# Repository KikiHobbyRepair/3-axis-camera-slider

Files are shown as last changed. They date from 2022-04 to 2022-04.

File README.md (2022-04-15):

# 3-axis-camera-slider
My newest DIY project is a 3 Axis motorised camera slicer. It is capable of handling smaller DSLR cameras and phones. It is portable because can be operated from a battery or alternatively from a DC power supply.

Link to the Youtube video: https://www.youtube.com/watch?v=ZBGcE2LZntI

I will also post a video later on about the full build process. I will put a link here as soon as it is published.

Parts list:
- 3D printed parts (preferred: PETG)
- openbuilds V wheel gentry. Most probably these are mostly the same but this is what I used: https://www.ebay.com/itm/403322339944
- 2040 V slot aluminum extrusion profile (I used 600mm long)
- 3 pcs Nema 17 stepper motors (I used 2pcs 0,9deg 2A and 1pc 1,8deg 2A version). High torque is needed especially for the tiliting mechanism
- 3pcs TMC2209 stepper motor drivers  https://www.aliexpress.com/item/33025652788.html?gatewayAdapt=glo2fra&spm=a2g0o.order_list.0.0.72a81802hnKEYC
- Bigtreetech extension board https://www.aliexpress.com/item/4001286167374.html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
- Arduino Nano (5V)
- 1,3" OLED screen (SPI version) https://www.aliexpress.com/item/32683739839.html?spm=a2g0o.order_list.0.0.72a81802AinbYI
- Rotary encoder: https://www.aliexpress.com/item/10000056483250.html?spm=a2g0o.order_list.0.0.72a81802AinbYI
- Momentary pushbutton: https://www.aliexpress.com/item/32965284265.html?spm=a2g0o.order_list.0.0.72a81802AinbYI
- GT2 Belt 6mm wide
- 20 teeth GT2 pulley with 5mm inner dia
- 20 teeth GT2 idler with 5mm inner dia
- M3 and M5 allen screws in different length (buy an assortment kit)
- M5 hammerhead nuts or T slot nuts
- M5 and M3 rectangluar nuts https://www.aliexpress.com/item/32964308882.html?spm=a2g0o.order_list.0.0.72a81802hnKEYC
- Some wires
- Rubber band for phone mount https://www.aliexpress.com/item/32751762287.html?spm=a2g0o.order_list.0.0.72a81802hnKEYC
- F623ZZ bearing 1 pcs
- Flange shaft coupler 2pcs (I have designed a 3D printed version too (STL available) but I prefer the metal here) https://www.amazon.de/gp/product/B0833PTFZM/ref=ppx_yo_dt_b_asin_title_o02_s00?ie=UTF8&psc=1
- etc

Buy Me a Coffe. If you find my work useful and valuable you can support the channel on the following link: https://www.buymeacoffee.com/kikihobbyrepair
3D file

DIY 3 Axis Motorized Camera Slider Thumbnail

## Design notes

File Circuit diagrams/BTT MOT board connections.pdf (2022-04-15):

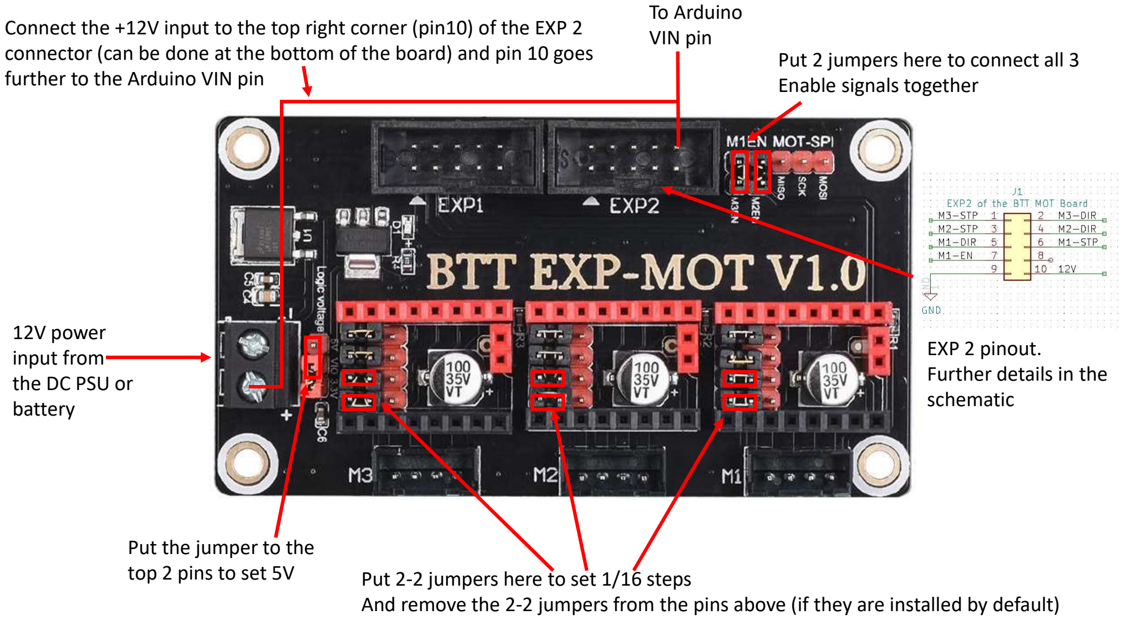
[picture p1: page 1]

Put 2 jumpers here to connect all 3 Enable signals together

Put 2-2 jumpers here to set 1/16 steps
And remove the 2-2 jumpers from the pins above (if they are installed by default)

Put the jumper to the
top 2 pins to set 5V

Connect the +12V input to the top right corner (pin10) of the EXP 2 connector (can be done at the bottom of the board) and pin 10 goes further to the Arduino VIN pin

EXP 2 pinout.
Further details in the
schematic

12V power
input from
the DC PSU or
battery

To Arduino
VIN pin

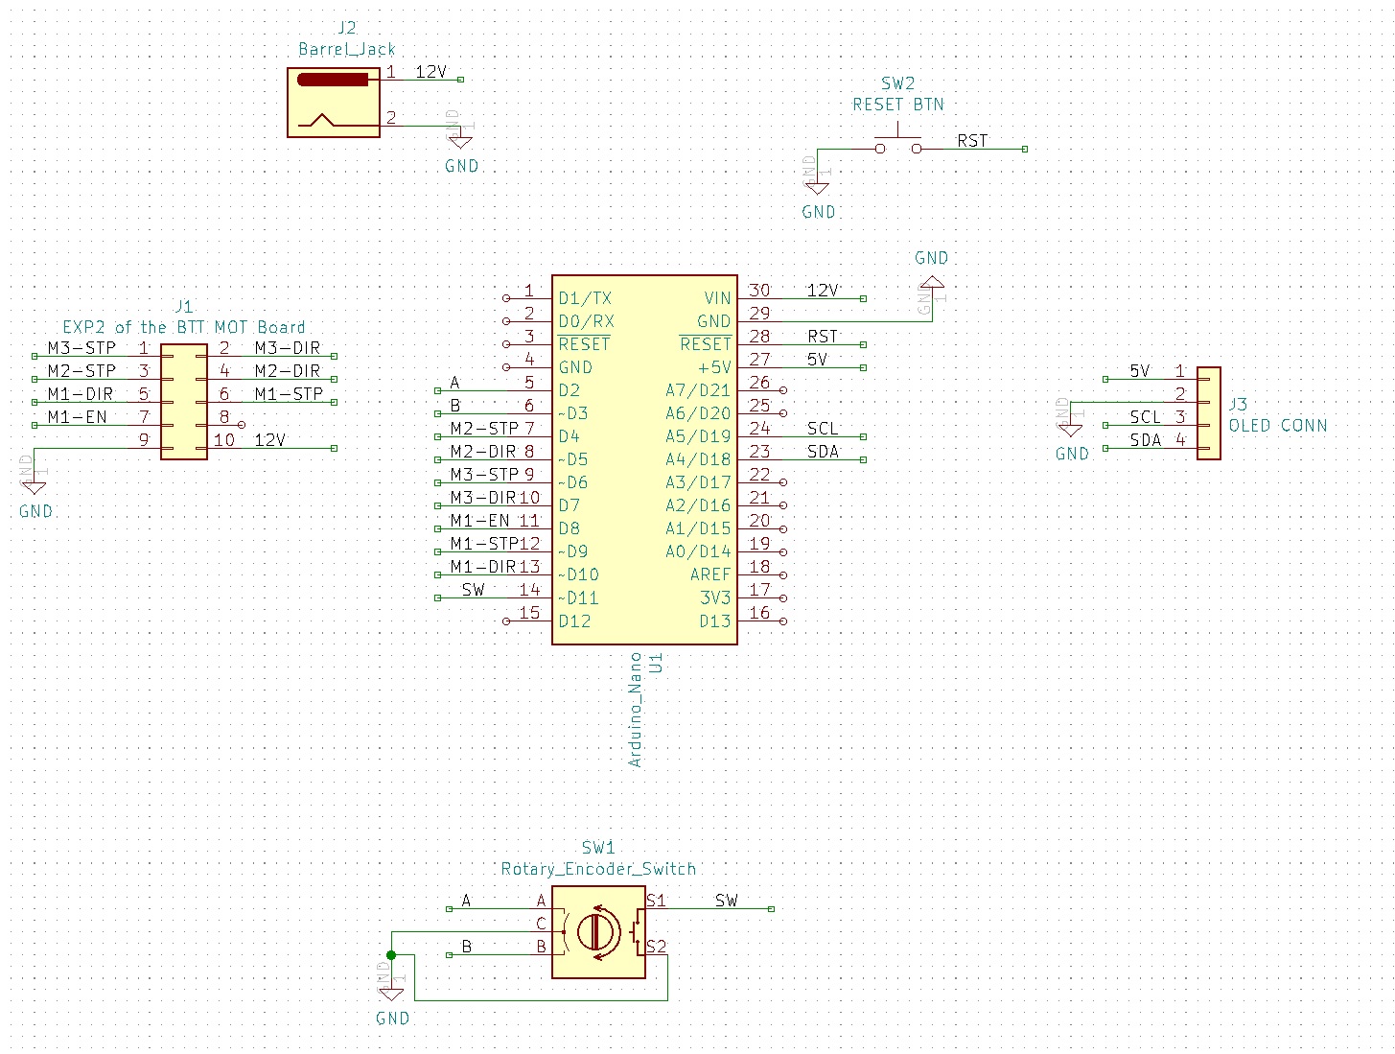
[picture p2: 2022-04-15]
Circuit diagrams/Schematic.jpg

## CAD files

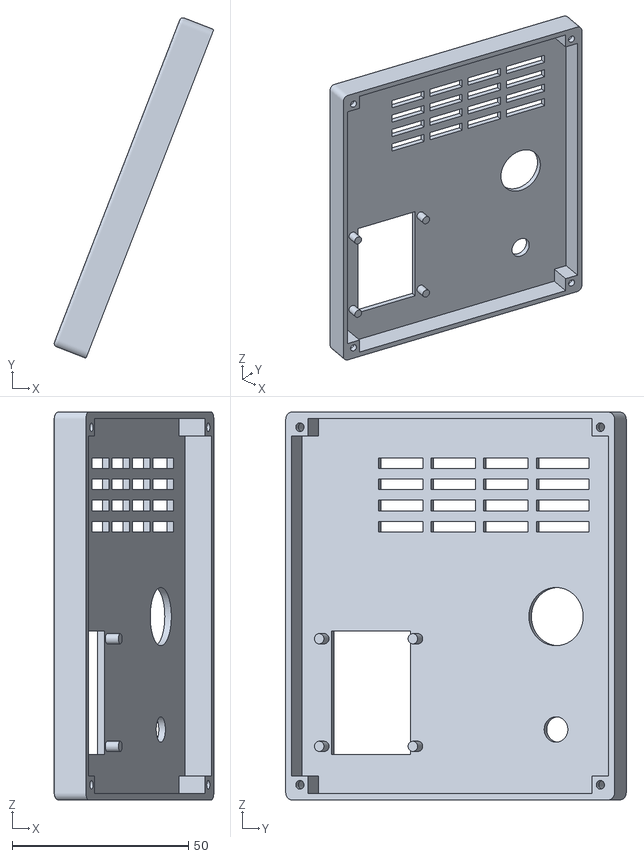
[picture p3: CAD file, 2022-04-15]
STL files/Box top.stl
45.3 x 96.5 x 110.0

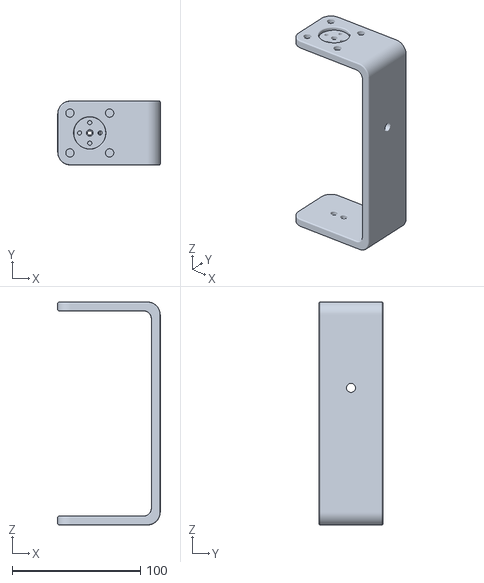
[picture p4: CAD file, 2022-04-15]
STL files/Camera mount.stl
80.0 x 50.0 x 174.0

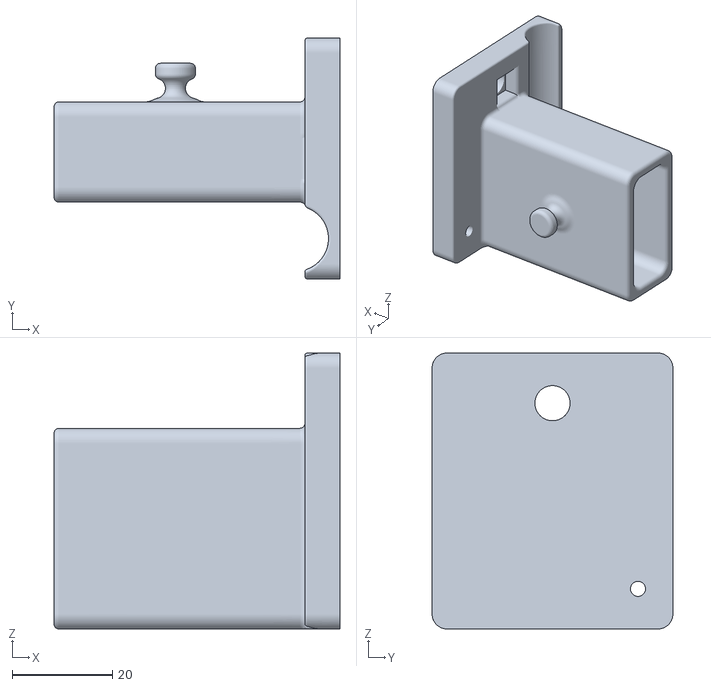
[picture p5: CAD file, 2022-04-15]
STL files/Phone holder bottom.stl
57.0 x 48.0 x 55.0

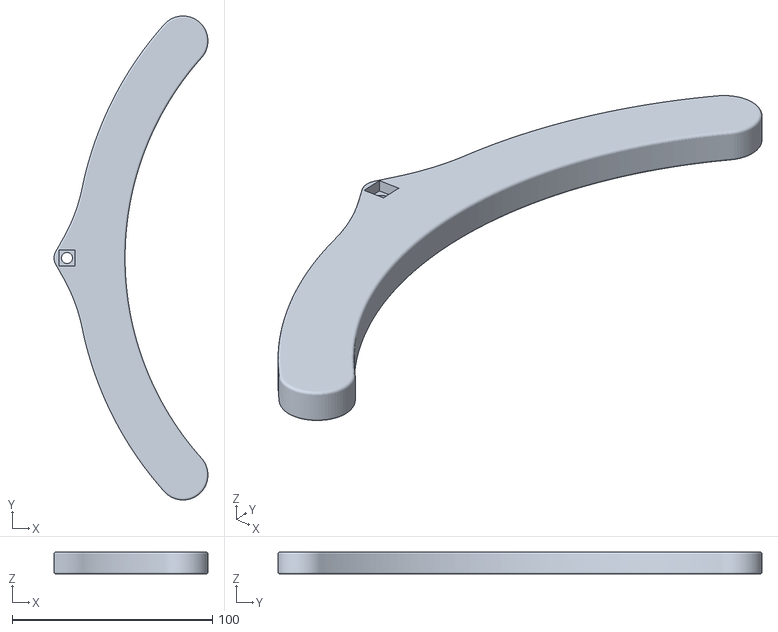
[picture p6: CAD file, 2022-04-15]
STL files/Leg 1.stl
76.9 x 241.7 x 10.9

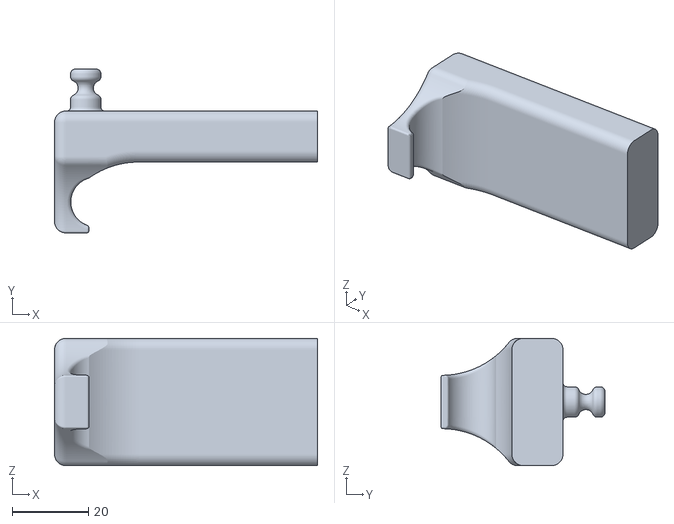
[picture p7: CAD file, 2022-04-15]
STL files/Phone holder top.stl
69.0 x 43.0 x 33.4

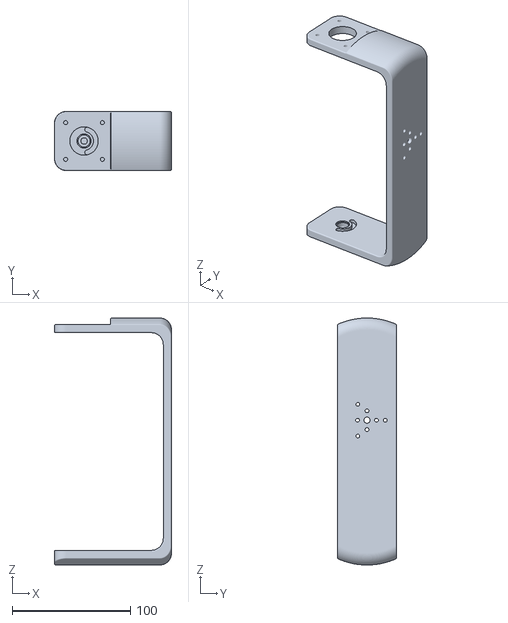
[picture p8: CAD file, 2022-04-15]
STL files/Top stepper holder.stl
99.0 x 50.0 x 208.9

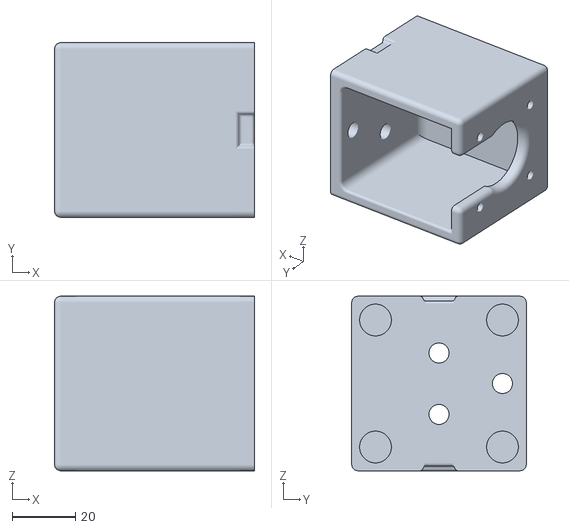
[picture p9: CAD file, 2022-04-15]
STL files/Bottom stepper holder 53mm inner.stl
63.0 x 55.0 x 55.0

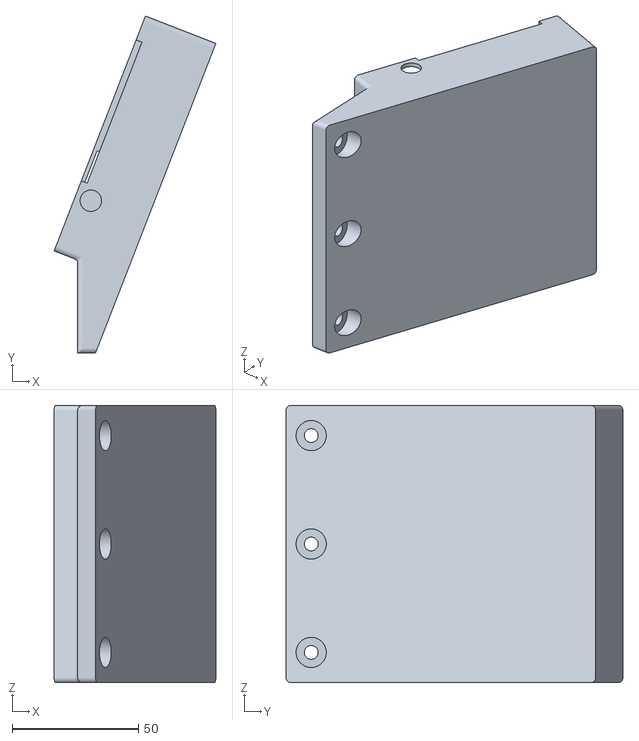
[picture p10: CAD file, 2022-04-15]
STL files/Box bottom.stl
64.2 x 133.7 x 110.0

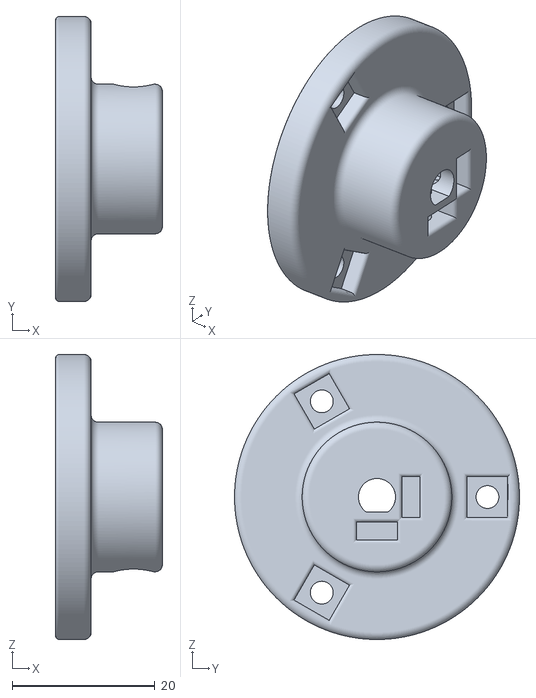
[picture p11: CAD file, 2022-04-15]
STL files/Shaft coupler.stl
15.0 x 40.0 x 40.0

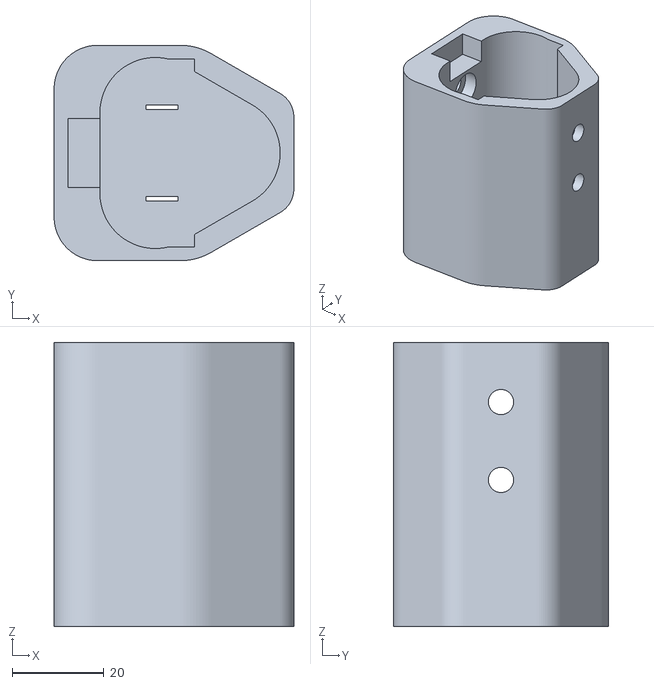
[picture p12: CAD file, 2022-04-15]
STL files/AEG battery holder.stl
52.4 x 47.0 x 62.0

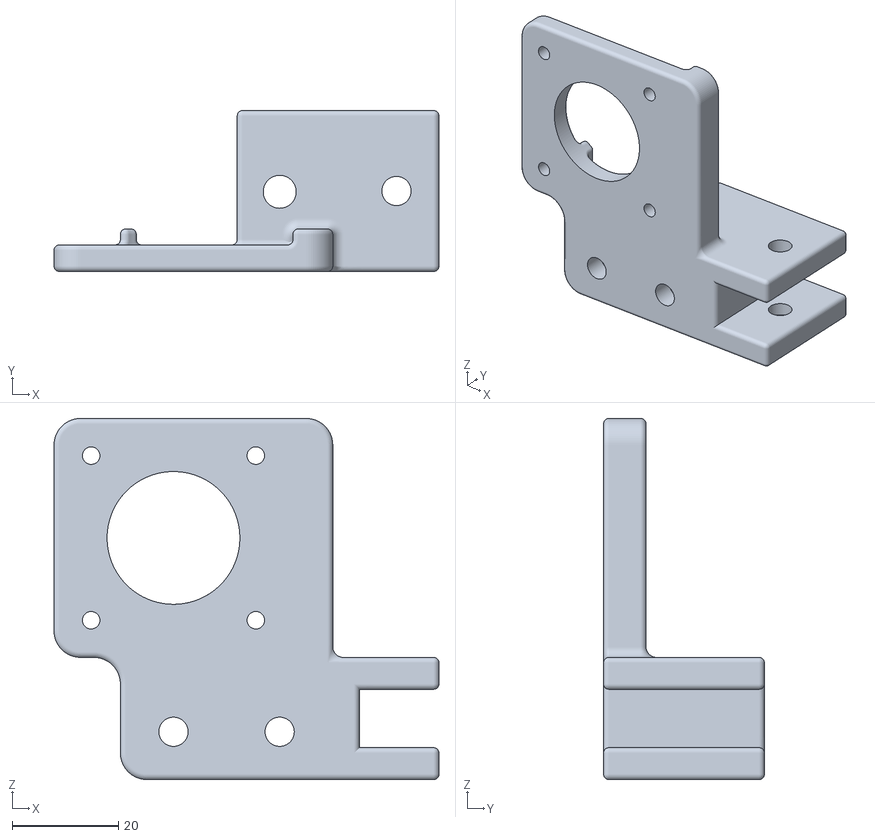
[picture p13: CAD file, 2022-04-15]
STL files/X stepper holder.stl
72.5 x 30.3 x 68.0

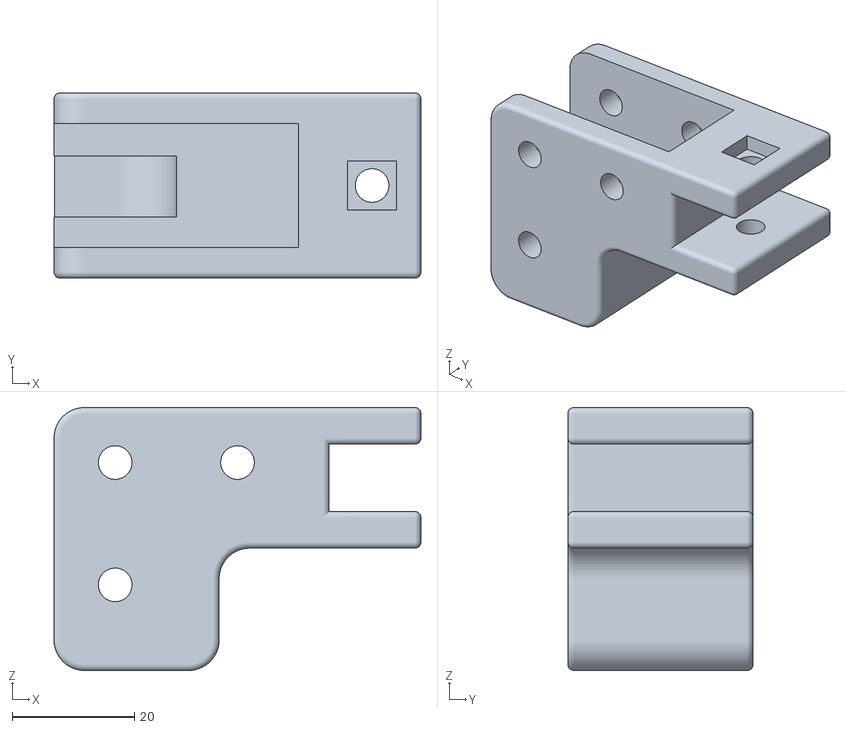
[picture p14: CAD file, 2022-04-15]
STL files/X idler holder.stl
60.0 x 30.3 x 43.0

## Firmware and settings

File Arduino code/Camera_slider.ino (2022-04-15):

//3 axis Camera Slider --- Kiki Hobby Repair
//Under development - USE IT AT YOUR OWN RISK!


#include <Arduino.h>
#include <Rotary.h>
#include <OneButton.h> 
#include <SpeedyStepper.h>
#include <U8g2lib.h>
#include <stdint.h>


Rotary r = Rotary(2, 3);
U8G2_SH1106_128X64_NONAME_1_HW_I2C u8g2(U8G2_R0, /* reset=*/ U8X8_PIN_NONE);  

#define enablePin       8                      //Motor enable pin
OneButton button(11,true);                     //Rotary Encoder Button
#define stepsPerMm      80                     //Slider step/mm (with 1.8deg motor)
#define stepPerDeg      17.77778               //rotate/tilt steps/degree (with 0.9deg motor)

const int MOTOR1_STEP_PIN = 9;
const int MOTOR1_DIRECTION_PIN = 10;
const int MOTOR2_STEP_PIN = 4;
const int MOTOR2_DIRECTION_PIN = 5;
const int MOTOR3_STEP_PIN = 6;
const int MOTOR3_DIRECTION_PIN = 7;

SpeedyStepper stepper1;
SpeedyStepper stepper2;
SpeedyStepper stepper3;

unsigned char result;
float encPos = 0;
int encMin = 0;
int encMax = 4;
int encSteps = 1;
int enter = 0;
int val = 0;
int slideDist = 0;
float rotAngle = 0;
float moveSpeed = 0;
float rotSpeed = 0;
float tiltSpeed = 0;
float tiltAngle = 0;



void setup() {
  
  u8g2.begin();
  u8g2.enableUTF8Print();
  pinMode(enablePin, OUTPUT);                        
  r.begin();
  PCICR |= (1 << PCIE2);
  PCMSK2 |= (1 << PCINT18) | (1 << PCINT19);
  sei();
  
  button.attachClick(click);
  stepper1.connectToPins(MOTOR1_STEP_PIN, MOTOR1_DIRECTION_PIN);
  stepper2.connectToPins(MOTOR2_STEP_PIN, MOTOR2_DIRECTION_PIN);
  stepper3.connectToPins(MOTOR3_STEP_PIN, MOTOR3_DIRECTION_PIN);
  stepper1.setStepsPerMillimeter(80);
  stepper2.setStepsPerRevolution(6400);
  stepper3.setStepsPerRevolution(6400);
  stepper1.setAccelerationInMillimetersPerSecondPerSecond(50);
  stepper2.setAccelerationInMillimetersPerSecondPerSecond(50);
  stepper3.setAccelerationInMillimetersPerSecondPerSecond(50);
  
  
}

void loop() {
  enter = 0;
  encMin = 0;
  encMax = 4;
  encSteps = 1;
  digitalWrite(enablePin, LOW);
  button.tick();
  
   u8g2.firstPage();
      do {
        
        u8g2.setFont(u8g2_font_osb18_tr);
        
           
        if (encPos == 0) {
          u8g2.setCursor(40, 40);  
          u8g2.print("Slide");
          if (enter == 1)
            {                     
              slide();
            }
          }
        
        else if  (encPos == 1) {
          
          u8g2.setCursor(15, 30);
          u8g2.print("Slide and"); 
          u8g2.setCursor(30, 55);
          u8g2.print("Rotate"); 
          if (enter == 1)
            {                     
              slideAndRotate();
            }   
          }
          
           else if  (encPos == 2) {
           u8g2.setCursor(40, 20);
          u8g2.print("Slide"); 
          u8g2.setCursor(5, 40);
          u8g2.print("Rotate and"); 
          u8g2.setCursor(46, 64);
          u8g2.print("Tilt"); 
          if (enter == 1)
            {                     
              slideAndRotateAndTilt();
            }  
          
          } 
        
          else if  (encPos == 3) {
           u8g2.setCursor(15, 30);
          u8g2.print("Slide and"); 
          u8g2.setCursor(46, 55);
          u8g2.print("Tilt"); 
          if (enter == 1)
            {                     
              slideAndTilt();
            } 
          }
        
          else if  (encPos == 4) {
           u8g2.setCursor(27, 30);
          u8g2.print("Object"); 
          u8g2.setCursor(13, 55);
          u8g2.print("Tracking");
          if (enter == 1)
            {                     
              objectTracking();
            } 
              
          }
        
   
      } while (u8g2.nextPage());    
          
}



ISR(PCINT2_vect) {
  result = r.process();
  if (result == DIR_NONE) {
    
  }
  else if (result == DIR_CW && encPos < encMax) {
    encPos = encPos + encSteps;
  }
  else if (result == DIR_CCW && encPos > encMin) {
    encPos = encPos - encSteps;
  }
  
}

void click()
  {
  enter = 1;
  }

void slide()
{
 encPos = 0;
 enter = 0;
 while (enter == 0)
  {
  button.tick();
  encMin = -450;
  encMax = 450;
  encSteps = 25;
  u8g2.firstPage();
      do {
  
          u8g2.setFont(u8g2_font_osb18_tr);
          u8g2.setCursor(15, 20);
          u8g2.print("Distance"); 
          u8g2.setCursor(15, 50);
          u8g2.print(encPos, 0);
          u8g2.setCursor(80, 50);
          u8g2.print("mm"); 
          

          slideDist = encPos;
          } while (u8g2.nextPage());
    
  }
    enter = 0;
    encPos = 10;

    
  while (enter == 0)
  {
  button.tick();
  encMin = 10;
  encMax = 3600;
  encSteps = 10;
  u8g2.firstPage();
      do {
  
          u8g2.setFont(u8g2_font_osb18_tr);
          u8g2.setCursor(15, 20);
          u8g2.print("Duration"); 
          u8g2.setCursor(15, 50);
          u8g2.print(encPos, 0);
          u8g2.setCursor(80, 50);
          u8g2.print("sec"); 
          moveSpeed = slideDist / encPos;
          } while (u8g2.nextPage());
  } 
  u8g2.firstPage();
      do {
  
          u8g2.setFont(u8g2_font_osb18_tr);
          u8g2.setCursor(15, 40);
          u8g2.print("Moving"); 
          
          } while (u8g2.nextPage());
  stepper1.setSpeedInMillimetersPerSecond(abs(moveSpeed));
  stepper1.setupRelativeMoveInMillimeters(slideDist);
    
  while(!stepper1.motionComplete()) 
        {
          stepper1.processMovement();
          
      
        }
  enter = 0;
  encPos = 0;
  moveSpeed = 0;
  slideDist = 0;
  
  }

  
void slideAndRotate()
{

 encPos = 0;
 enter = 0;
 while (enter == 0)
  {
  button.tick();
  encMin = -450;
  encMax = 450;
  encSteps = 25;
  u8g2.firstPage();
      do {
  
          u8g2.setFont(u8g2_font_osb18_tr);
          u8g2.setCursor(15, 20);
          u8g2.print("Distance"); 
          u8g2.setCursor(15, 50);
          u8g2.print(encPos, 0);
          u8g2.setCursor(80, 50);
          u8g2.print("mm"); 
          slideDist = encPos;
          } while (u8g2.nextPage());
    
  }
    enter = 0;
    encPos = 0;
    
  while (enter == 0)
  {
  button.tick();
  encMin = -120;
  encMax =  120;
  encSteps = 10;
  u8g2.firstPage();
      do {
  
          u8g2.setFont(u8g2_font_osb18_tr);
          u8g2.setCursor(0, 20);
          u8g2.print("Rot. Angle"); 
          u8g2.setCursor(15, 50);
          u8g2.print(encPos, 0);
          u8g2.setCursor(80, 50);
          u8g2.print("deg"); 
          rotAngle = encPos/360;
          } while (u8g2.nextPage());
  }

        enter = 0;
        encPos = 10;
        
  while (enter == 0)
  {
  button.tick();
  encMin = 10;
  encMax = 3600;
  encSteps = 10;
  u8g2.firstPage();
      do {
  
          u8g2.setFont(u8g2_font_osb18_tr);
          u8g2.setCursor(15, 20);
          u8g2.print("Duration"); 
          u8g2.setCursor(15, 50);
          u8g2.print(encPos, 0);
          u8g2.setCursor(80, 50);
          u8g2.print("sec"); 
          moveSpeed = slideDist / encPos;
          rotSpeed = rotAngle / encPos;
          } while (u8g2.nextPage());
  } 
  u8g2.firstPage();
      do {
  
          u8g2.setFont(u8g2_font_osb18_tr);
          u8g2.setCursor(15, 40);
          u8g2.print("Moving"); 
          
          } while (u8g2.nextPage());
  stepper1.setSpeedInMillimetersPerSecond(abs(moveSpeed));
  stepper1.setupRelativeMoveInMillimeters(slideDist);
  stepper2.setSpeedInRevolutionsPerSecond(abs(rotSpeed));
  stepper2.setupRelativeMoveInRevolutions(rotAngle);
  
  while((!stepper1.motionComplete()|| !stepper2.motionComplete())) 
        {
          stepper1.processMovement();
          stepper2.processMovement();
        }
  
  
  enter = 0;
  encPos = 0;
  moveSpeed = 0;
  slideDist = 0;
  
   
  }



void slideAndRotateAndTilt()
{
  encPos = 0;
 enter = 0;
 while (enter == 0)
  {
  button.tick();
  encMin = -450;
  encMax = 450;
  encSteps = 25;
  u8g2.firstPage();
      do {
  
          u8g2.setFont(u8g2_font_osb18_tr);
          u8g2.setCursor(15, 20);
          u8g2.print("Distance"); 
          u8g2.setCursor(15, 50);
          u8g2.print(encPos, 0);
          u8g2.setCursor(80, 50);
          u8g2.print("mm"); 
          slideDist = encPos;
          } while (u8g2.nextPage());
    
  }
    enter = 0;
    encPos = 0;
    
  while (enter == 0)
  {
  button.tick();
  encMin = -120;
  encMax =  120;
  encSteps = 10;
  u8g2.firstPage();
      do {
  
          u8g2.setFont(u8g2_font_osb18_tr);
          u8g2.setCursor(0, 20);
          u8g2.print("Rot. Angle"); 
          u8g2.setCursor(15, 50);
          u8g2.print(encPos, 0);
          u8g2.setCursor(80, 50);
          u8g2.print("deg"); 
          rotAngle = encPos/360;
          } while (u8g2.nextPage());
  }

        enter = 0;
        encPos = 0;

  while (enter == 0)
  {
  button.tick();
  encMin = -120;
  encMax =  120;
  encSteps = 10;
  u8g2.firstPage();
      do {
  
          u8g2.setFont(u8g2_font_osb18_tr);
          u8g2.setCursor(0, 20);
          u8g2.print("Tilt. Angle"); 
          u8g2.setCursor(15, 50);
          u8g2.print(encPos, 0);
          u8g2.setCursor(80, 50);
          u8g2.print("deg"); 
          tiltAngle = -encPos/360;
          } while (u8g2.nextPage());
  }

        enter = 0;
        encPos = 10;

        
  while (enter == 0)
  {
  button.tick();
  encMin = 10;
  encMax = 3600;
  encSteps = 10;
  u8g2.firstPage();
      do {
  
          u8g2.setFont(u8g2_font_osb18_tr);
          u8g2.setCursor(15, 20);
          u8g2.print("Duration"); 
          u8g2.setCursor(15, 50);
          u8g2.print(encPos, 0);
          u8g2.setCursor(80, 50);
          u8g2.print("sec"); 
          moveSpeed = slideDist / encPos;
          rotSpeed = rotAngle / encPos;
          tiltSpeed = tiltAngle / encPos;
          } while (u8g2.nextPage());
  } 
  u8g2.firstPage();
      do {
  
          u8g2.setFont(u8g2_font_osb18_tr);
          u8g2.setCursor(15, 40);
          u8g2.print("Moving"); 
          
          } while (u8g2.nextPage());
  stepper1.setSpeedInMillimetersPerSecond(abs(moveSpeed));
  stepper1.setupRelativeMoveInMillimeters(slideDist);
  stepper2.setSpeedInRevolutionsPerSecond(abs(rotSpeed));
  stepper2.setupRelativeMoveInRevolutions(rotAngle);
  stepper3.setSpeedInRevolutionsPerSecond(abs(tiltSpeed));
  stepper3.setupRelativeMoveInRevolutions(tiltAngle);
  
  
  while(!stepper1.motionComplete()|| !stepper2.motionComplete() || !stepper3.motionComplete())
        {
          stepper1.processMovement();
          stepper2.processMovement();
          stepper3.processMovement();
        }
  
  
  enter = 0;
  encPos = 0;
  moveSpeed = 0;
  slideDist = 0;
  tiltSpeed = 0;
  rotSpeed = 0;
  
  
   
  }  

void slideAndTilt()
{
  encPos = 0;
 enter = 0;
 while (enter == 0)
  {
  button.tick();
  encMin = -450;
  encMax = 450;
  encSteps = 25;
  u8g2.firstPage();
      do {
  
          u8g2.setFont(u8g2_font_osb18_tr);
          u8g2.setCursor(15, 20);
          u8g2.print("Distance"); 
          u8g2.setCursor(15, 50);
          u8g2.print(encPos, 0);
          u8g2.setCursor(80, 50);
          u8g2.print("mm"); 
          slideDist = encPos;
          } while (u8g2.nextPage());
    
  }
    enter = 0;
    encPos = 0;
    
 

  while (enter == 0)
  {
  button.tick();
  encMin = -120;
  encMax =  120;
  encSteps = 10;
  u8g2.firstPage();
      do {
  
          u8g2.setFont(u8g2_font_osb18_tr);
          u8g2.setCursor(0, 20);
          u8g2.print("Tilt. Angle"); 
          u8g2.setCursor(15, 50);
          u8g2.print(encPos, 0);
          u8g2.setCursor(80, 50);
          u8g2.print("deg"); 
          tiltAngle = -encPos/360;
          } while (u8g2.nextPage());
  }

        enter = 0;
        encPos = 10;

        
  while (enter == 0)
  {
  button.tick();
  encMin = 10;
  encMax = 3600;
  encSteps = 10;
  u8g2.firstPage();
      do {
  
          u8g2.setFont(u8g2_font_osb18_tr);
          u8g2.setCursor(15, 20);
          u8g2.print("Duration"); 
          u8g2.setCursor(15, 50);
          u8g2.print(encPos, 0);
          u8g2.setCursor(80, 50);
          u8g2.print("sec"); 
          moveSpeed = slideDist / encPos;
          tiltSpeed = tiltAngle / encPos;
          } while (u8g2.nextPage());
  } 
  u8g2.firstPage();
      do {
  
          u8g2.setFont(u8g2_font_osb18_tr);
          u8g2.setCursor(15, 40);
          u8g2.print("Moving"); 
          
          } while (u8g2.nextPage());
  stepper1.setSpeedInMillimetersPerSecond(abs(moveSpeed));
  stepper1.setupRelativeMoveInMillimeters(slideDist);
  stepper3.setSpeedInRevolutionsPerSecond(abs(tiltSpeed));
  stepper3.setupRelativeMoveInRevolutions(tiltAngle);
  
  
  while(!stepper1.motionComplete() || !stepper3.motionComplete())
        {
          stepper1.processMovement();
          
          stepper3.processMovement();
        }
  
  
  enter = 0;
  encPos = 0;
  moveSpeed = 0;
  slideDist = 0;
  tiltSpeed = 0;
  
  }  

void objectTracking()
{
  
  }    
  
